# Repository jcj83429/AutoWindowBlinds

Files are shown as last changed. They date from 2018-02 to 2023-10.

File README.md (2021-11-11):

# AutoWindowBlinds
automatic window blind controller based on the Teensy 3.2 board

Automatically open the window blinds when it's bright outside, and close it when it's dark.

I use duff2013's Snooze library to put the system in lower power sleep and only periodically wake up, and cut power to unneeded components when the system is in low power sleep using a relay. The idle power draw measured at the battery power input is about 50uA. It should last at least a year on 4 rechargeable AA batteries.

Use commit d1b25d4b122fbc02c98a257f9ddc8b473f4e621c (2019-04-30) of the Snooze library. The latest version has a different API.

* schematic/ contains the KiCad schematic for the circuit
* CAD/ contains the FreeCad design for the 3D printed adapter that goes between the motor and the stick the motor needs to turn

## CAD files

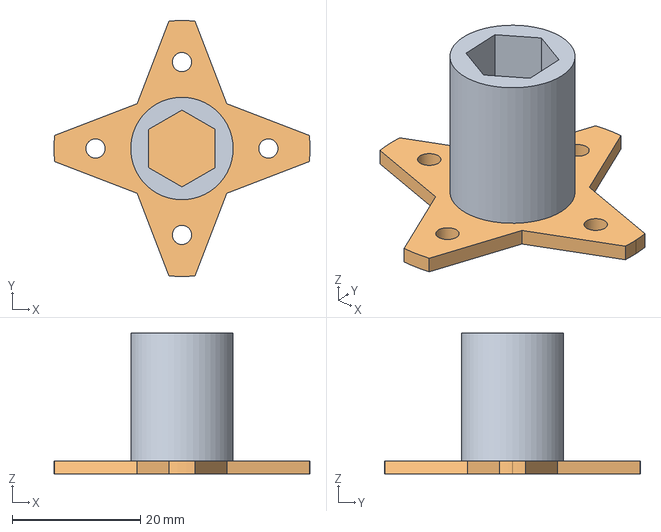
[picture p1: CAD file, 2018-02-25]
CAD/blind.FCStd
40.0 x 40.0 x 22.0 mm

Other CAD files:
CAD/blind.stl

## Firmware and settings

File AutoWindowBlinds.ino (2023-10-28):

#include <Wire.h>
#include "SparkFun_VEML6030_Ambient_Light_Sensor.h"

// using snooze breaks USB serial print
// disable snooze for debugging
#define USE_SNOOZE 1

#define MOTOR_SPEED 240
#define ROTATIONS_TO_OPEN 4
#define ROTATION_SENSOR_TIMEOUT 8000

#define ERR_LOW_BATT 1
#define ERR_ROTATION_FAIL 2
#define ERR_SENSOR_INIT 3

#define MOTOR_FORWARD 1
#define MOTOR_REVERSE -1
#define MOTOR_STOP 0

#define MOTOR_DIR_CURTAIN_OPEN MOTOR_REVERSE
#define MOTOR_DIR_CURTAIN_CLOSE MOTOR_FORWARD

// to save power, only turn on HV circuits (>3.3v) when needed
// HV circuits include motor driver and hall sensor
#define PIN_HV_EN_RELAY 6
#define PIN_MOTOR_FORWARD 10
#define PIN_MOTOR_REVERSE 9
#define PIN_HALL_SENSOR_READ 8

// push button for manually toggling open/close
#define PIN_MANUAL_SW 11

#define VEML6030_ADDR 0x48

enum CurtainState {
  CURTAIN_CLOSED = 0, 
  CURTAIN_OPEN = 1,
};

enum LightState {
  DARK = 0,
  LIGHT = 1,
};

////////////////////////////////////////////////////////////////
// GLOBALS
////////////////////////////////////////////////////////////////

#if USE_SNOOZE
#include <Snooze.h>
// Load drivers
SnoozeTimer snoozeTimer;
SnoozeDigital snoozeDigital;
// install drivers to a SnoozeBlock
SnoozeBlock snoozeConfig(snoozeTimer, snoozeDigital);
#endif

// Assume the system powers on with the curtain closed!!!
CurtainState currentCurtainState = CURTAIN_CLOSED;
int currentCurtainPosition = 0;
int openPosition = ROTATIONS_TO_OPEN;
LightState currentLightState = DARK;

// default light and dark threshold
float dbLuxThreshDark = -5;
float dbLuxThreshLight = 5;

// brightness distribution in the last 24 hours.
// each bucket is 1 dbLux.
// every 24 hours, the resistance thresholds are adjusted based on the brightness stat.
#define DBLUX_STAT_BUCKETS 100
// The sensor can sense 0.0036 to 120000 lux (-24.4 to +50.8 dbLux)
#define DBLUX_STAT_BUCKET_OFFSET 25;
int dbLuxStat[DBLUX_STAT_BUCKETS] = {0};
int dbLuxStatSamples = 0;
unsigned long lastThresholdAdjTime = 0;

// The data is noisy below 0 dbLux, so the threshold must be set higher than 0 dbLux
#define DBLUX_MEDIAN_LIMIT 0

SparkFun_Ambient_Light light(VEML6030_ADDR);

float gainTimeSettings[10][2] = {
  {2, 800},   // 0.0036
  {2, 400},   // 0.0072
  {2, 200},   // 0.0144
  {2, 100},   // 0.0288
  {2, 50},    // 0.0576
  {2, 25},    // 0.1152
  {1, 25},    // 0.2304
  {0.25, 50}, // 0.4608
  {0.25, 25}, // 0.9216
  {0.125, 25},// 1.8432
};

const int numGainTimeSettings = 10;
int curGainTimeSetting = 5;

////////////////////////////////////////////////////////////////
// FUNCTIONS
////////////////////////////////////////////////////////////////

void halt(int error){
  setMotorDirection(MOTOR_STOP, 0);
  digitalWrite(PIN_HV_EN_RELAY, LOW);
  
  digitalWrite(LED_BUILTIN, LOW);
  sleepDispatch(500);
  
  while(true){
    for(int i=0; i<error; i++){
      digitalWrite(LED_BUILTIN, HIGH);
      sleepDispatch(500);
      digitalWrite(LED_BUILTIN, LOW);
      sleepDispatch(500);
    }
    sleepDispatch(1000);
  }
}

void setGainTimeSetting(int index){
  curGainTimeSetting = index;
  light.setGain(gainTimeSettings[index][0]);
  light.setIntegTime(gainTimeSettings[index][1]);
}

float readLuxAutoRange(){
  uint16_t rawValue = light._readRegister(AMBIENT_LIGHT_DATA_REG);
  bool powSaveDisabled = false;
  while((rawValue < 100 && curGainTimeSetting > 0) || (rawValue > 10000 && curGainTimeSetting < numGainTimeSettings - 1)){
    if(!powSaveDisabled){
      light.disablePowSave();
      sleepDispatch(4000);
      powSaveDisabled = true;
    }
    int oldIntegrationTime = gainTimeSettings[curGainTimeSetting][1];
    if(rawValue < 100){
      if(rawValue < 50 && curGainTimeSetting >= 2){
        setGainTimeSetting(curGainTimeSetting - 2);
      }else{
        setGainTimeSetting(curGainTimeSetting - 1);
      }
    }else{
      setGainTimeSetting(curGainTimeSetting + 1);
    }
    Serial.printf("adjusting resolution to %d\n", curGainTimeSetting);
    sleepDispatch(oldIntegrationTime);
    sleepDispatch(gainTimeSettings[curGainTimeSetting][1] * 1.2);
    rawValue = light._readRegister(AMBIENT_LIGHT_DATA_REG);
  }
  if(powSaveDisabled){
    light.enablePowSave();
  }
  float lux = light._calculateLux(rawValue);
  if(lux > 1000){
    lux = light._luxCompensation(lux);
  }
  return lux;
}

// Wiring: PIN_MANUAL_SW - push button - GND
// PIN_MANUAL_SW is in INPUT_PULLUP mode
bool manualSwPressed(){
  return !digitalRead(PIN_MANUAL_SW);
}

bool readHallSensor(){
  return digitalRead(PIN_HALL_SENSOR_READ);
}

void setMotorDirection(int direction, int motorSpeed){
  switch(direction){
  case MOTOR_FORWARD:
    analogWrite(PIN_MOTOR_REVERSE, 0);
    analogWrite(PIN_MOTOR_FORWARD, motorSpeed);
    break;
  case MOTOR_REVERSE:
    analogWrite(PIN_MOTOR_FORWARD, 0);
    analogWrite(PIN_MOTOR_REVERSE, motorSpeed);
    break;
  case MOTOR_STOP:
    analogWrite(PIN_MOTOR_FORWARD, 0);
    analogWrite(PIN_MOTOR_REVERSE, 0);
    break;
  }
}

void applyCurrentState(int motorSpeed){
  Serial.println(__FUNCTION__);

  int positionDelta;
  int targetPosition;
  int motorDirection;
  if(currentCurtainState == CURTAIN_OPEN){
    targetPosition = openPosition;
  }else{
    targetPosition = 0;
  }

  if(targetPosition == currentCurtainPosition){
    return;
  }

  Serial.print("  currentCurtainPosition=");
  Serial.println(currentCurtainPosition);
  Serial.print("  targetPosition=");
  Serial.println(targetPosition);
  Serial.print("  positionDelta=");
  Serial.println(positionDelta);

  digitalWrite(PIN_HV_EN_RELAY, HIGH);
  delay(1000);

  if(targetPosition > currentCurtainPosition){
    setMotorDirection(MOTOR_DIR_CURTAIN_OPEN, motorSpeed);
    unsigned long rotationStartTime = millis();
    bool lastHallSensorState = readHallSensor();
    // When opening, go to targetposition+1 then come back to targetPosition
    // This way the motor always stops where it would be when rotating in the close direction.
    while(currentCurtainPosition < targetPosition + 1){
      bool newHallSensorState = readHallSensor();
      unsigned long currentTime = millis();
      digitalWrite(LED_BUILTIN, newHallSensorState);

      if(currentTime - rotationStartTime > ROTATION_SENSOR_TIMEOUT){
        Serial.println("HALT: MOTOR OR ROTATION SENSOR FAILED");
        halt(ERR_ROTATION_FAIL);
      }
      
      if(newHallSensorState == 1 && lastHallSensorState == 0){
        currentCurtainPosition++;
        Serial.print("  currentCurtainPosition=");
        Serial.println(currentCurtainPosition);
        rotationStartTime = millis();
      }
      lastHallSensorState = newHallSensorState;
    }
    delay(300); // make sure the magnet is clear of the hall sensor
  }

  if(targetPosition < currentCurtainPosition){
    setMotorDirection(MOTOR_DIR_CURTAIN_CLOSE, motorSpeed);
    unsigned long rotationStartTime = millis();
    bool lastHallSensorState = readHallSensor();
    // When opening, go to targetposition+1 then come back to targetPosition
    // This way the motor always stops near end of the position.
    while(currentCurtainPosition > targetPosition){
      bool newHallSensorState = readHallSensor();
      unsigned long currentTime = millis();
      digitalWrite(LED_BUILTIN, newHallSensorState);

      if(currentTime - rotationStartTime > ROTATION_SENSOR_TIMEOUT){
        Serial.println("HALT: MOTOR OR ROTATION SENSOR FAILED");
        halt(ERR_ROTATION_FAIL);
      }
      
      if(newHallSensorState == 1 && lastHallSensorState == 0){
        currentCurtainPosition--;
        Serial.print("  currentCurtainPosition=");
        Serial.println(currentCurtainPosition);
        rotationStartTime = millis();
      }
      lastHallSensorState = newHallSensorState;
    }
    delay(300); // make sure the magnet is clear of the hall sensor
  }

  setMotorDirection(MOTOR_STOP, 0);
  digitalWrite(PIN_HV_EN_RELAY, LOW);
}

void handleLightState(LightState state){
  if(state == currentLightState){
    return;
  }

  if(state == LIGHT){
    currentCurtainState = CURTAIN_OPEN;
  }else{
    currentCurtainState = CURTAIN_CLOSED;
  }

  currentLightState = state;
}

// Adjust the position for the CURTAIN_OPEN state.
// brighter -> less open
void adjustOpenPosition(float dbLux) {
  int minPos, maxPos;
  if(dbLux > 34){
    minPos = 2;
    maxPos = 2;
  }else if(dbLux > 32){
    minPos = 2;
    maxPos = 3;
  }else if(dbLux > 30){
    minPos = 3;
    maxPos = 3;
  }else if(dbLux > 28){
    minPos = 3;
    maxPos = ROTATIONS_TO_OPEN;
  }else{
    minPos = ROTATIONS_TO_OPEN;
    maxPos = ROTATIONS_TO_OPEN;
  }
  openPosition = max(minPos, min(maxPos, openPosition));
}

void doLightStat(float dbLux){
  int bucket = dbLux + DBLUX_STAT_BUCKET_OFFSET;
  if(bucket >= DBLUX_STAT_BUCKETS){
    bucket = DBLUX_STAT_BUCKETS - 1;
  }else if (bucket < 0){
    bucket = 0;
  }
  dbLuxStat[bucket]++;
  dbLuxStatSamples++;

  const unsigned long dayInMs = 24 * 3600 * 1000;
  if(millis() - lastThresholdAdjTime > dayInMs){
    int newThreshold = 0;
    int cumulativeSamples = 0;
    for(int i=0; i<DBLUX_STAT_BUCKETS; i++){
      cumulativeSamples += dbLuxStat[i];
      if(cumulativeSamples >= dbLuxStatSamples/2){
        newThreshold = i - DBLUX_STAT_BUCKET_OFFSET;
        break;
      }
    }

    if(newThreshold < DBLUX_MEDIAN_LIMIT){
      newThreshold = DBLUX_MEDIAN_LIMIT;
    }

    dbLuxThreshDark = dbLuxThreshDark * 0.5 + (newThreshold - 5) * 0.5;
    dbLuxThreshLight = dbLuxThreshLight * 0.5 + (newThreshold + 5) * 0.5;

    dbLuxStatSamples = 0;
    for(int i=0; i<DBLUX_STAT_BUCKETS; i++){
      dbLuxStat[i] = 0;
    }
    lastThresholdAdjTime += dayInMs;
  }
}

void handleDbLux(float dbLux){
  if(dbLux < dbLuxThreshDark){
    handleLightState(DARK);
  }else if(dbLux > dbLuxThreshLight){
    handleLightState(LIGHT);
  }
  adjustOpenPosition(dbLux);
  applyCurrentState(MOTOR_SPEED);

  doLightStat(dbLux);
}

void sleepDispatch(uint16_t sleepMs){
#if USE_SNOOZE
  /********************************************************
  * Set Low Power Timer wake up in milliseconds.
  ********************************************************/
  snoozeTimer.setTimer(sleepMs);// milliseconds
  /********************************************************
  * feed the sleep function its wakeup parameters. Then go 
  * to deepSleep.
  ********************************************************/
  Snooze.hibernate(snoozeConfig);
#else
  unsigned long t0 = millis();
  while(millis() - t0 < sleepMs){
    // simulate Snooze's wake on digital pin
    if(manualSwPressed()){
      break; 
    }
  }
#endif
}

// see K20P64M72SF1RM.pdf
// This may be useless. The highest LV warning threshold supported is 3.0V.
// This is below the min rated voltage for the L293D H-bridge and SS443A hall sensor.
// The system may error out and halt due to rotation failure before the 3V3 line drops to 3.0V.
void configureLowVoltageWarning(){
  // choose high detect threshold, enable LV reset
  PMC_LVDSC1 = PMC_LVDSC1_LVDV(1) | PMC_LVDSC1_LVDRE;
  // choose highest warning threshold
  PMC_LVDSC2 = PMC_LVDSC2_LVWV(3);
}

bool lowVoltageWarningTripped(){
  return !!(PMC_LVDSC2 & PMC_LVDSC2_LVWF);
}

void setup() {
  // Wait a bit before turning on low voltage detection.
  // Otherwise the LVD may trigger immediately and require a restart.
  delay(100);
  configureLowVoltageWarning();
  pinMode(LED_BUILTIN, OUTPUT);
  pinMode(PIN_HV_EN_RELAY, OUTPUT);
  pinMode(PIN_MOTOR_FORWARD, OUTPUT);
  pinMode(PIN_MOTOR_REVERSE, OUTPUT);
  pinMode(PIN_MANUAL_SW, INPUT_PULLUP);
  pinMode(PIN_HALL_SENSOR_READ, INPUT_PULLUP);
  analogWriteFrequency(PIN_MOTOR_FORWARD, 375000);
  
  Serial.begin(9600);

#if USE_SNOOZE
  snoozeDigital.pinMode(PIN_MANUAL_SW, INPUT_PULLUP, FALLING);
#endif

  Wire.begin();
  if(light.begin()){
    Serial.println("Ready to sense some light!");
  }else{
    Serial.println("Could not communicate with the sensor!");
    halt(ERR_SENSOR_INIT);
  }
}

void loop() {
  if(lowVoltageWarningTripped()){
    halt(ERR_LOW_BATT);
  }

  float lux, dbLux;
  
  digitalWrite(LED_BUILTIN, HIGH);


  // manual toggle
  if(manualSwPressed()){
    currentCurtainState = static_cast<CurtainState>(currentCurtainState ^ 1);
    applyCurrentState(255);
    goto endloop;
  }
  
  lux = readLuxAutoRange();
  dbLux = 10.0 * log10(max(lux, 0.0036));
  Serial.print("dbLux=");
  Serial.print(dbLux);
  Serial.print(" light=");
  Serial.print(dbLuxThreshLight);
  Serial.print(" dark=");
  Serial.println(dbLuxThreshDark);
  handleDbLux(dbLux);
  

endloop:
  digitalWrite(LED_BUILTIN, LOW);
  sleepDispatch(60000);
}

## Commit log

2018-02-25 add code and CAD files
    [blind.FCStd, blind.stl]
2018-02-25 add schematic
    [schematic.kicad_pcb, schematic.sch]
2018-04-14 enable low voltage detection, tweak constants,
    full rotation speed when toggled manually
2021-11-11 switch to a sparkfun veml6030 light sensor
    The photoresistor has poor resolution at low light levels
2023-01-05 battery related changes
    - wait 100ms before turning on low voltage detection so it won't trip immediately
    - shorten the max tolerated time per motor rotation to avoid overdischarging rechargeable batteries.
    [AutoWindowBlinds.ino]
2023-10-28 update schematic
    replace analog photoresistor with digital light sensor.
    this is long overdue
